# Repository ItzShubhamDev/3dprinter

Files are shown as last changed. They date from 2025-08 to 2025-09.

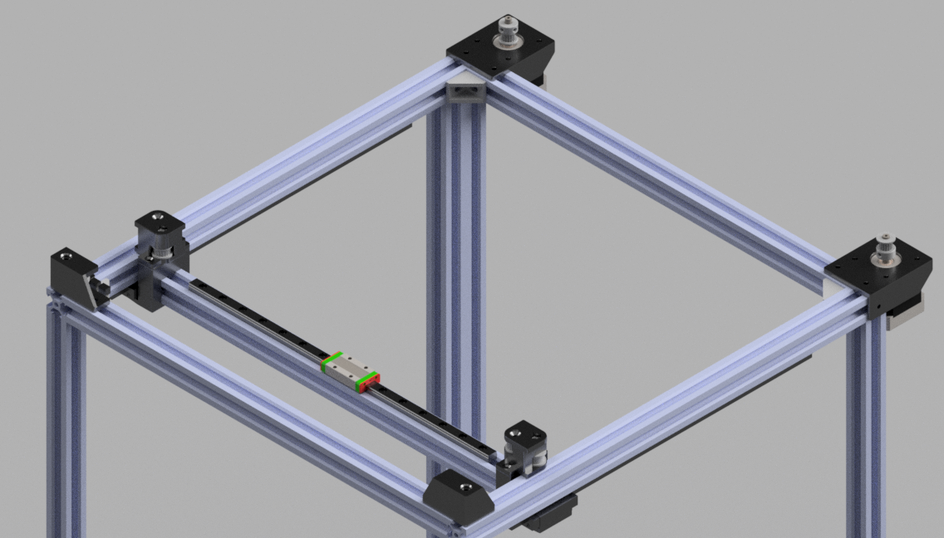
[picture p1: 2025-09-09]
images/8.png

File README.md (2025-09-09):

# Yenvo X3

A Custom Large CoreXY 3D Printer having a Print Volume of 36,000 cm³ powered by Bigtreetech SKRat V1.0 and Marling firmware.

My and my friend wanted to print something large without sliccing it, so I decided to make this printer as part of Highway.
This repository contains information related to 3D Printer, including the 3D parts models, firmware, BOM, all models imported into the design.

## Features

- **Faster building** - CoreXY printers are in general faster than Cartesian printers
- **Less space** - Unlike Cartesian printers in which Z-axis moves horizonatally, Z-axis moves vertically so it takes less space
- **Large build area 300x300x400 mm³** - Common printers around this price are mostly 250³ mm³.
- **Easy to maintain and upgrade** - If anything gives wrong just replace that part.
- **Budget friendly** - Only around 300$ can be reduced more if in a metro city by buying parts locally.

### Printer







### Structure 



### Z-Axis



### XY Motion



### Print Area



### Motherboard, Power Supply and Display



## Bill Of Materials

|Name |Quantity|Price(INR)|Cost(INR)|Cost(USD)|Source |
|---|---|---|---|---|---|
|Titan extruder kit 0.4mm Mk8 nozzle 1.75mm filament for 3D printer|1 |2199 |2199 |24.189 |https://novo3d.in/titan-extruder-kit/ |
|42 stepper motor nema17 40mm for 3D printer |4 |579 |2316 |25.476 |https://novo3d.in/42-stepper-motor-nema17/ |
|Aluminium Profiles 2020 V Slot Extrusion black anodized - 380mm |6 |136.01 |816.08 |8.97688  |https://novo3d.in/aluminium-profiles-2020/ |
|Aluminium Profiles 2020 V Slot Extrusion black anodized - 480mm |4 |171.81 |687.23 |7.55953  |https://novo3d.in/aluminium-profiles-2020/ |
|Aluminium profile 2040 V Slot extrusion black anodized - 460mm |1 |390.54 |390.54 |4.29594  |https://novo3d.in/aluminium-profile-2040/ |
|Aluminium Profiles 2020 V Slot Extrusion black anodized - 420mm |2 |150.33 |300.66 |3.30726  |https://novo3d.in/aluminium-profiles-2020/ |
|Linear Guide Rail MGN Blocks CNC Linear Rail Slide - MGN12H |2 |499 |998 |10.978 |https://novo3d.in/linear-guide-rail/?attribute_type=MGN12H |
|MGN12H Linear Rail Guide Carriage 30cm (without block) |2 |849 |1698 |18.678 |https://novo3d.in/mgn12h-linear-rail/?attribute_size=30cmattribute_type=without+block |
|MGN9H Linear Rails 30cm (without block) |1 |799 |799 |8.789 |https://novo3d.in/mgn9h-linear-rail/?attribute_length=30cmattribute_block=without+block |
|Linear Guide Rail MGN Blocks CNC Linear Rail Slide - MGN9H |1 |479 |479 |5.269 |https://novo3d.in/linear-guide-rail/?attribute_type=MGN9H |
|10mm Smooth Rod Stainless Steel - 500mm |4 |265 |1060 |11.66 |https://novo3d.in/10mm-smooth-rod/?attribute_length=500mm |
|Flexible coupling 5x8mm |2 |55 |110 |1.21 |https://novo3d.in/flexible-coupling-5x8mm/ |
|LM10UU 10mm linear bearing |4 |45 |180 |1.98 |https://novo3d.in/lm10uu-10mm-bearing/ |
|Single Start Lead Screw 2mm pitch - 400mm |2 |239 |478 |5.258 |https://novo3d.in/single-start-lead-screw/?attribute_size=400mm |
|GT2 6mm Timing belt Steel Core - 1000cm |1 |690 |690 |7.59 |https://novo3d.in/gt2-6mm-belt/ |
|Motor Pulley GT2 16 teeth 5mm bore |2 |35 |70 |0.77 |https://novo3d.in/motor-pulley/?attribute_no-of-teeth=16+teethattribute_bore=5mm |
|Idler pulley 6mm without teeth 5mm bore |2 |69 |138 |1.518 |https://novo3d.in/idler-pulley/?attribute_type=6mm+without+teeth |
|Idler pulley 6mm with teeth 5mm bore |6 |69 |414 |4.554 |https://novo3d.in/idler-pulley-6mm/?attribute_belt-width=6mm+with+teeth |
|Mini Limit Switch 3 pin SPDT L-type |3 |13.5 |40.5 |0.4455 |https://novo3d.in/mini-limit-switch/?attribute_type=L-+type |
|Bigtreetech Mini 12864 Display V2.0 |1 |1099 |1099 |12.089 |https://novo3d.in/bigtreetech-mini-12864-display/ |
|Bigtreetech SKRat V1.0 control board 32bit 64MHz |1 |3689 |3689 |40.579 |https://novo3d.in/bigtreetech-skrat-v1-0/ |
|Bed Leveling Nut Set M3 |4 |29 |116 |1.276 |https://novo3d.in/bed-leveling-nutset/?attribute_type=M3+nut+set |
|Heat bed 310mm 12V with 100cm cable |1 |1799 |1799 |19.789 |https://novo3d.in/heat-bed-310mm/?attribute_voltage=12vattribute_type=Heat+bed+with+100cm+cable|
|Meanwell Power Supply 12V 30A |1 |2999 |2999 |32.989 |https://novo3d.in/mean-well-power-supply/?attribute_voltage=12V+30A |
|Misc. (Screw, Nuts, Bolts, Wires, etc.) |1 | | |25 | |
| | | |23566.01 |284.22611| |

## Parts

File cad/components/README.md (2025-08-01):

## Models Info 

### Created By Me

- 5mmx8mm Coupling Shaft
- 8mm Threaded Rod 400mm
- 10mm Smooth Rod 500mm
- Brass Circle Nut
- Display
- Double Head Pulley Holder
- Extruder Motor Holder
- GT2 20 Teeth
- Hotend Extruder joint
- Hotend Holder
- Hotend Stand
- Idle Pulley 20 teeth
- L Joint
- LM10UU
- Motor Holder
- Sensor Case Z
- Sensor Case
- SK10 Shaft
- Teethless Pulley
- XY Joint
- Z Motion Motor Holder

### Modified By Me

- 2020 Aluminium Profile
- 2040 Aluminium Profile
- MGN9H
- MGN12C_With_Rail
- NEMA 17

### External

- 4010 - Blower Assembly
- Bigtreetech Mini12864 V1.0-3D
- Bondtech dual gear extruder
- D2F-01L
- EL90050--STD--24V 360W Power Supply 
- V6 Short Highspeed Hotend v10

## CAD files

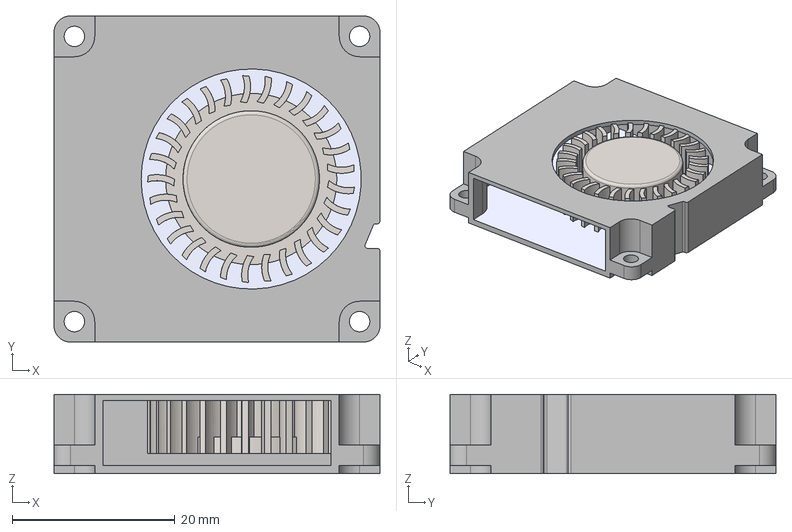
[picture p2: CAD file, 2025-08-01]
cad/components/4010 - Blower Assembly.step
40.0 x 40.0 x 9.75 mm

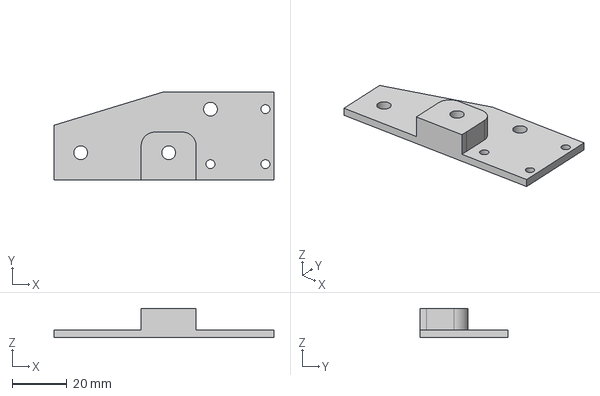
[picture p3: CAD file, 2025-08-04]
cad/components/Pulley Joint.step
80.0 x 32.2 x 10.6 mm

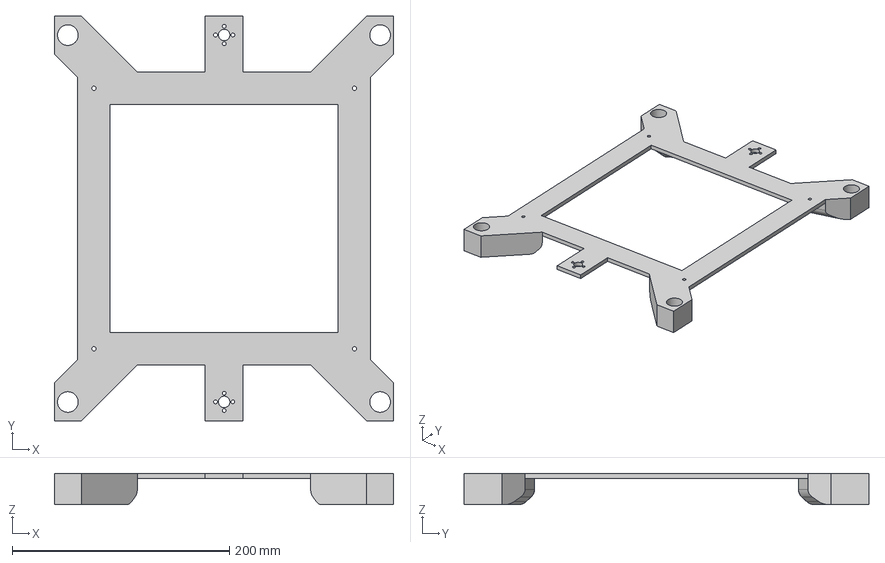
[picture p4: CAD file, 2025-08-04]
cad/production/Heatbed support.step
312.7 x 373.1 x 29.0 mm

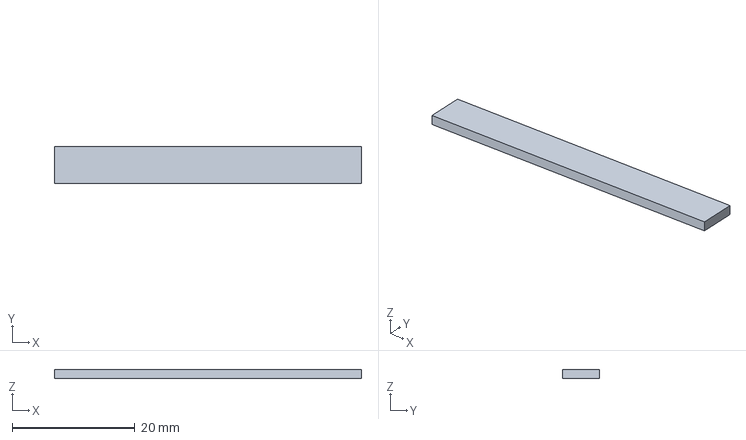
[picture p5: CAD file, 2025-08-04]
cad/components/Simple Belt.step
50.0 x 6.00 x 1.50 mm

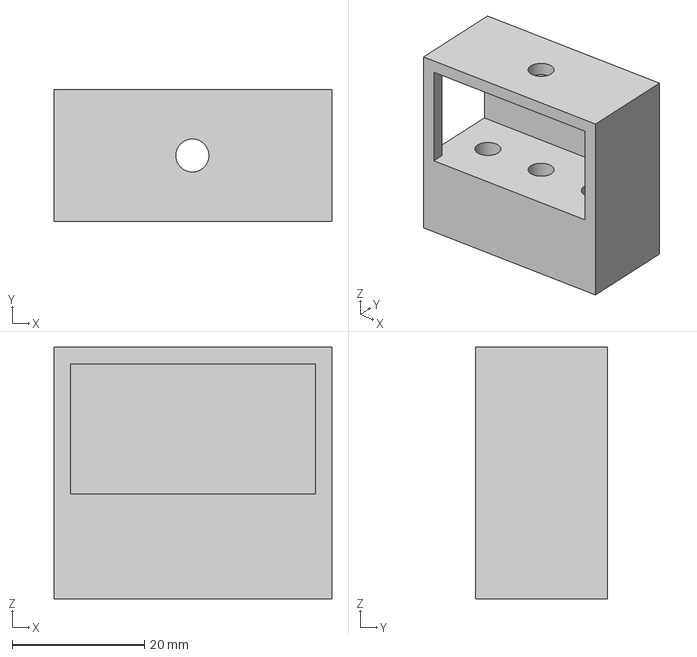
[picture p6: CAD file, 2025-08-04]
cad/production/Pulley Case.step
42.0 x 20.0 x 38.0 mm

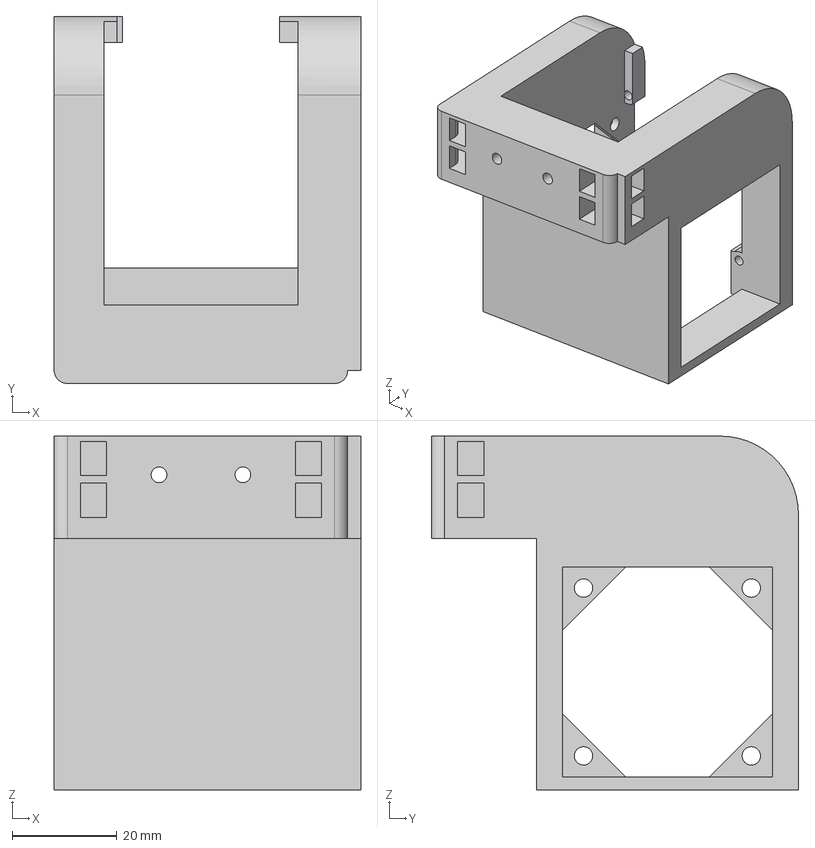
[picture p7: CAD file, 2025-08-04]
cad/components/Hotend Case.step
58.5 x 70.0 x 67.5 mm

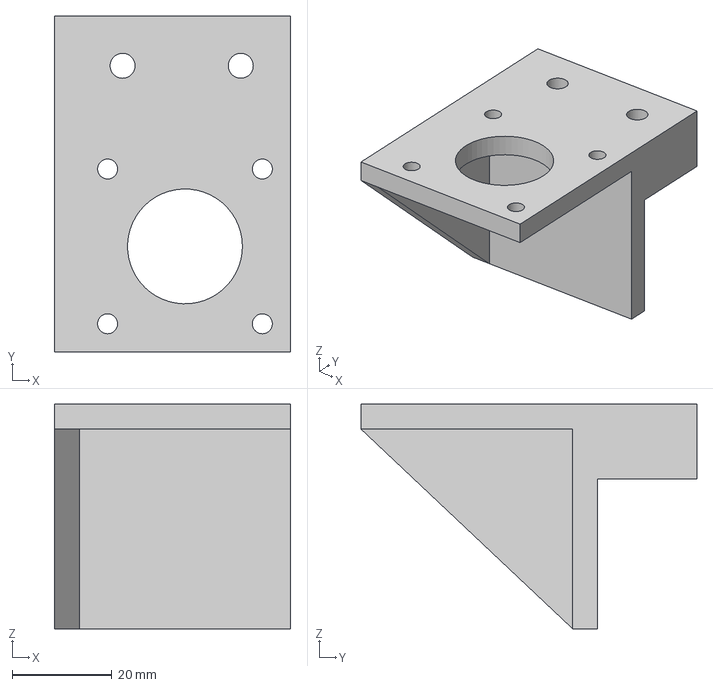
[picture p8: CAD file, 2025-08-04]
cad/components/Nema17 Holder.step
47.3 x 67.3 x 45.0 mm

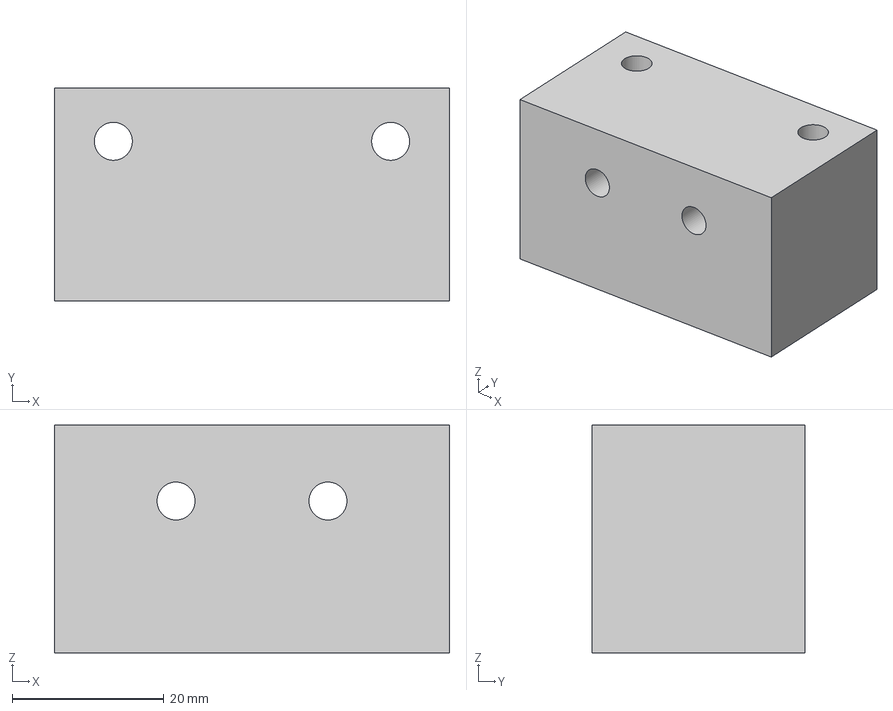
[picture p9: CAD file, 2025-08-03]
cad/production/KFL08Joint.step
52.0 x 28.0 x 30.0 mm

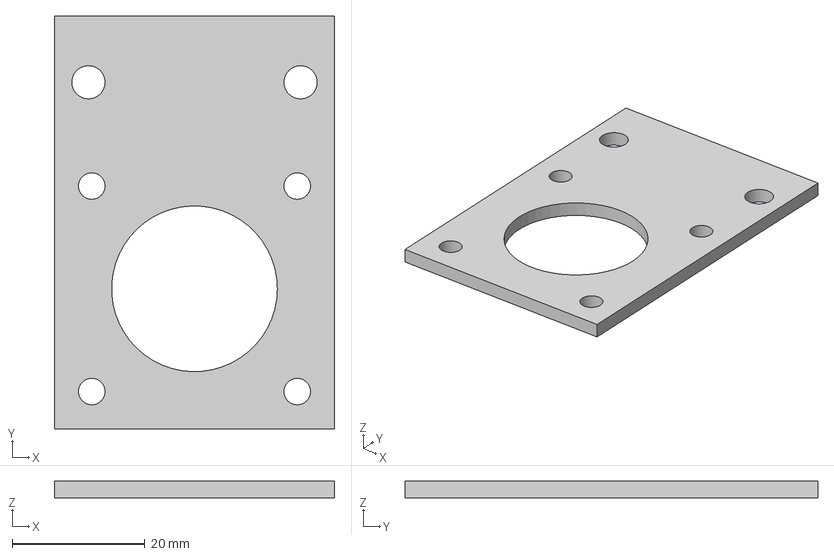
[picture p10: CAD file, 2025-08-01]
cad/production/Z Motion Motor Holder.step
42.3 x 62.3 x 2.50 mm

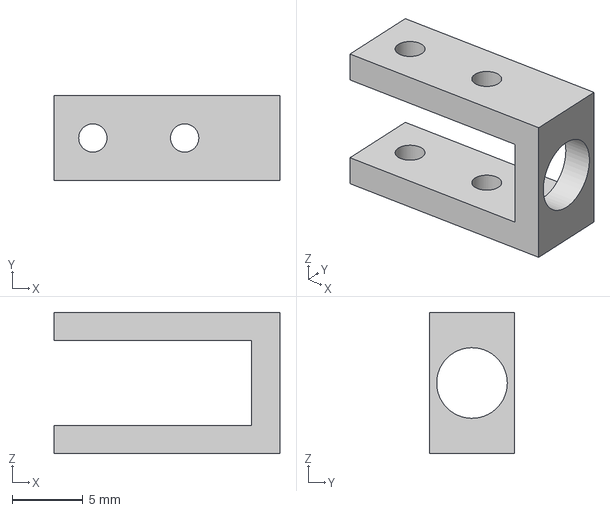
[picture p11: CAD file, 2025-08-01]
cad/production/Sensor Case.step
16.0 x 6.00 x 10.0 mm

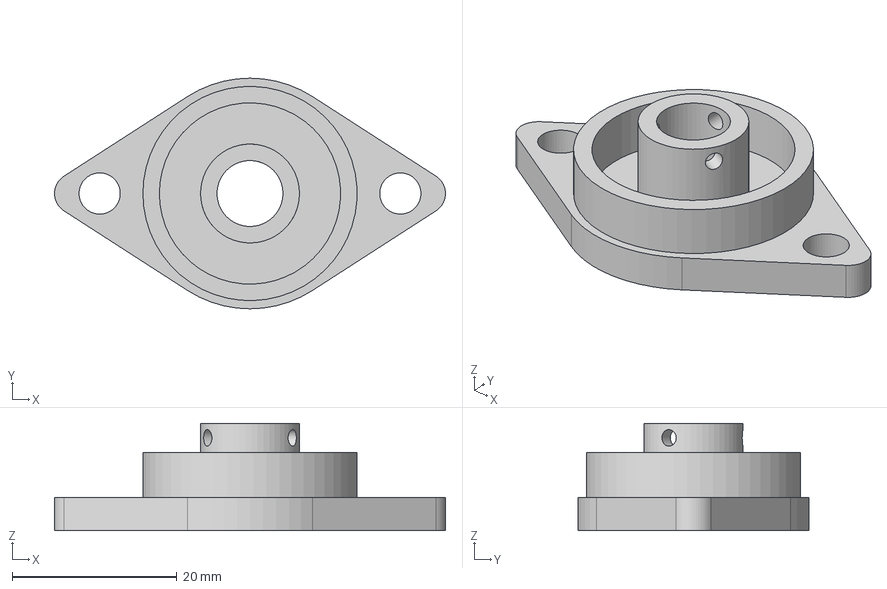
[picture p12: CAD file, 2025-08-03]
cad/components/KFL08.step
47.5 x 28.0 x 13.0 mm

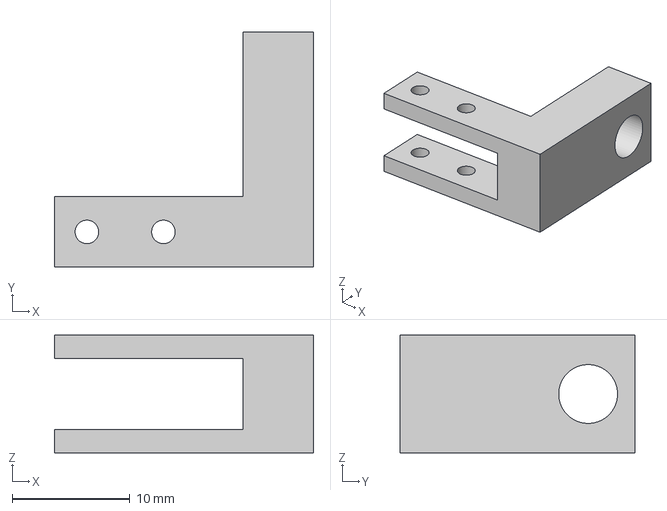
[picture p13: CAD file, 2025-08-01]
cad/production/Sensor Case Z.step
22.0 x 20.0 x 10.0 mm

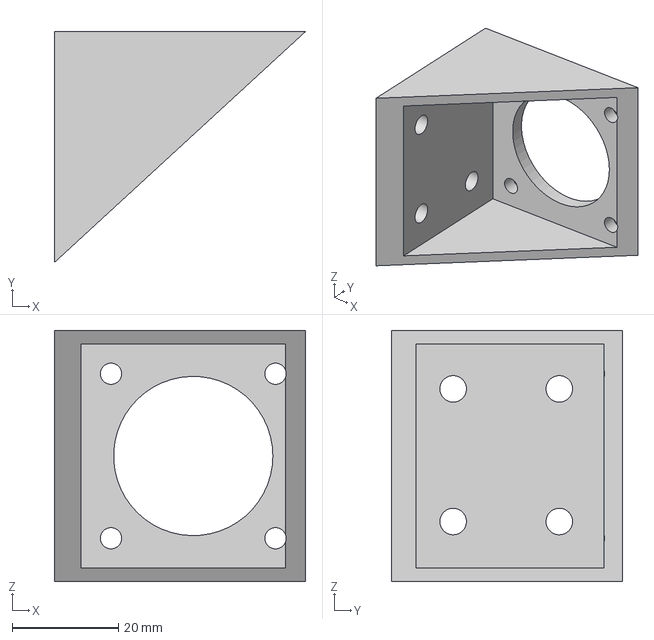
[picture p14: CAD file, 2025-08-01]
cad/production/Extruder Motor Holder.step
47.3 x 43.5 x 47.3 mm

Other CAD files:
cad/components/10mm Smooth Rod 500mm.step
cad/components/2020 Aluminium Profile.step
cad/components/2040 Aluminium Profile.step
cad/components/5mmx8mm Coupling Shaft.step
cad/components/8mm Threaded Rod 400mm.step
cad/components/Brass Circle Nut.step
cad/components/D2F-01L.step
cad/components/GT2 20 Teeth.step
cad/components/Hotend Extruder joint.step
cad/components/Hotend Stand.step
cad/components/Idle Pulley 20 teeth.step
cad/components/L Joint.step
cad/components/LM10UU.step
cad/components/MGN12C_With_Rail.step
cad/components/MGN9H.step
cad/components/NEMA 17.step
cad/components/Nema17 Holder (1).step
cad/components/Pulley Case (1).step
cad/components/Pulley Joint (1).step
cad/components/SK10 Shaft.step
cad/components/Teethless Pulley.step
cad/production/Nema17 Holder (1).step
cad/production/Pulley Case (1).step

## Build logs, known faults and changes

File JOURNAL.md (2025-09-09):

---
Title: "Yenvo X3"
Author: "Shubham"
Description: "A CoreXY 3D Printer having a large build volume 300x300x400 mm³"
Created_at: "2024-07-28"
Total Time Spent: 95 hours
---

# Yenvo X3

## Overview

| Section | Details |
| --- | --- |
| Design Choices | Decided to go with **CoreXY** over Cartesian / Delta printer for a combination of speed and stability.<br/> Wanted to make a large **400x400x400 mm³** printer but limited to **300x300x400 mm³** due to unavailibity of large heatbeds still enabling printing large parts without joints. <br /> Decided to use **2020 and 2040** Aluminium Extrusions for the sturcture to provide structural rigidity and ease to joints. <br /> Initially thought on using **V-Wheels** for the XY motion, went with **Linear Rails** after learning about the drawbacks of using V-Wheels. <br /> Used **2x Lead Screw Threaded Rods** both joint with one stepper motor each along with **4x Smooth Rods** for the movement of Z-Axis. <br /> For the movement of Hotend assembly along X-axis decided to go with **Linear Rails** too might be an overkill but would provide much precise movement <br /> For the extruder favoured went with **Direct drive**. <br /> As for the hotend, I would most likely be using a **0.4mm Volcano Hotend** to allow fast print times fitting the large build volume. <br /> As for the motherboard I would most likely be using [SKRat V1](https://novo3d.in/bigtreetech-skrat-v1-0/) due to it's pricing and connectors for 2 Z-Axis motors (which I might add in future) or [SKR MINI E3 V3](https://novo3d.in/skr-mini-e3/) which doesn't have separate connections for 2 Z-Axis motors but supports parallel connection with same pricing as SKRat V1 and additional silent features and larger heat sink for better heat management. |
| Challenges Faced | The most problematic issue I faced was **Components Sourcing**, whenever I decided to go with a part either it was unavailable or was for ridiculous high price on the local vendors. And purchasing them overseas although cheaper would end up being higher price due to shippings and customs. <br /> The second problem I faced was dimensions issue since at start I had no idea what the dimensions would each part be, I had to made some changes almost every time I added a new component.|
| References | I got to learn a lot about CoreXY Printers builds from amazing videos like [TechBuilder's DIY Guide](https://www.youtube.com/watch?v=yuAN5AzEWCg) and [3DJake's DIY Guide](https://www.youtube.com/watch?v=NMfFirtB1D4), apart from these I also watched and read articles few more to learn more. <br /> I also used some 3D models from [GrabCAD](https://grabcad.com/). |
| Learning | Throughout the whole build I learnt a lot more about Fusion 360, how to use each and every tools. Apart from that I also learned how to design sketches effectively for an easier 3d model. Not only that I also got to know how to manage various instances of same component without creating a link between them. |

## Journal

### Day 1 (28 July)

**Log 1** - Started the day by gathering a brief information on different types of 3D Printers, their advantages, disadvantages and working principle. (CoreXY, Cartesian, Delta, etc.). Initially thought of making a large size printer 400x400x400 mm³ CoreXY printer due to high speeds prints but was restricted to 300x300 mm² beds, so ended up with 300x300x300 mm³ still large height to allow larger builds to made without any joints. Gained a lot of information from various sources especially
[TechBuilder's CoreXY Guide](https://www.youtube.com/watch?v=yuAN5AzEWCg) and [3DJake's CoreXY Guide](https://www.youtube.com/watch?v=NMfFirtB1D4).
Didn't did anything in CAD yet.

**Time Spent** - 8 hours

### Day 2 (29 July)

**Log 1** - Watched some more tutorials, regarding different CoreXY builds, component placements and different parts that can be used for getting the same effect. After some discussion with one of my friends, I decided to go with a 300x300x400 mm³ with the same bed size but still allowing models upto 400mm print without joints.

As for the CAD I started making up the basic structure of the Printer by using just basic cuboids.



**Time Spent** - 6 hours

**Log 2** - After the basic structure completed, I redesigned the base structure with the use of 8x 2020 for the base and the height and 4x 2040 Aluminium Profiles for the top..
 


**Time Spent** - 4 hours

### Day 3 (30 July)

**Log 1** - Added the Stepper Motors, Shafts and 400mm Threaded Rods. The threaded rods appreared to be at height higher than the profiles due to starting ~50-60mm above ground surface because of the motor and shaft.
So recreated the structure with more height in the Z Axis. And created some 3D models for the Linear shafts.





**Time Spent** - 5 hours

**Log 2** - After looking out various Gantries I decided to make my printer unique by using V-Wheels instead of linear rails as I was already using Aluminium Profiles and linear rails were also very expensive.

Added linear Smooth rods and shafts. <br />
Create wheels model and added the wheels, also added the plates for the wheels.
Added 300mm Aluminium Profile which felt short which I would be fixing tommorrow.




**Time spent** - 5 hours

### Day 4 (31 July)

**Log 1** - As the 300mm Aluminium Profile felt short, adjusted it's length and created and added linear rails on side of the Aluminium profile, for the movement of hotend assembly on the X-Axis.
And created L-Joints for the corners.





**Time spent** - 5 hours

**Log 2** - While gathering more information about V-wheels mouting and proper usage, found out many resources recommending not to use V-wheels for XY motions due to their bad performance and wear-tear, which makes sense why no one used V-wheels in the first place, so I eventually decided to go with the linear rails.
Had to recontruct from scratch in a new Document due to the fact components were linked and couldn't resize components at different places.

        


**Time spent** - 4 hours

**Log 3** -
Created 3 models for the pulleys required.
The Pulleys section filled up a lot of confusion inside me, I was to search for Idler Teeth Pulley, but was just searching Teeth Pulley, which I never found. After releasing this I created a model for the Idler teeth pulley as well.





**Time spent** - 4 hours

**Log 4** - The 3D models for some components were missing that includes pulleys, hotend cover and some other parts too. So, I created the 3D models for them and included them into the design.



**Time spent** - 4 hours

**Log 5** - Some other components that were missing like heatbeds, linear bearing, so created and added them as well.



**Time spent** - 3 hours

## Post Submission Journals

### Day 5 (1 August)

**Log 1** - The heatbed I previously added was just a temporary and I made that it a hurry so I forgot the heatbed needs to be separated and the bottom part should be a separate entity screwed onto the Lead Screw and onto the Linear bearings. So fixed that. And also added mounting plates and brackets for the Motion and extrusions motors respectively.



**Time spent** - 4 hours

### Day 6 (3 August)

**Log 1** - The top part of the Threaded rods appeared to be flowing, so to fix that created a 3D model for threaded rod joint and a 3D printed part to screw it onto the the Aluminium profiles.



**Time spent** - 2 hours

### Day 7 (4 August)

**Log 1** - Fixed gantry by adjusting the levels of pulleys and change pulleys types. The hotend extruder also seemed very odd, so redesigned it again.
The Heatbed support felt a bit wierd when I thought of thier movement, so decided to extend the base to cover the full motion bearings

**Time Spent** - 7 hours




### Day 8 (1 September)

**Log 1** - After being called out, fixed some components, added filament spools holder, made a case / holder for power supply and added a mounting plate for the controller board.

**Time Spent** - 6 hours





### Day 9, 10, 11 & 12  

**Time Spent** - 25 hours

My current model had a flaws so I recreated the whole model by improving and implementing a lot of changes which could have severily impacted the performance and/or functioning of the printer which includes but are not limited to:
- Split all non printable parts into 2 halves.
- Modified the Heat bed support plate
- Modified the case for Display
- Redesigned the gantry, inspired by a 3d printer built in real life and working smoothly
- Removed support from leadscrew
- Switched to Direct drive instead of Bowden drive
and a various small changes.

Special thanks to Tanishq & Raygen for helping me identifing and fixed those issues.





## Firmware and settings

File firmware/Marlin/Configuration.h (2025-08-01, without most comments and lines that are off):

#pragma once
#define CONFIG_EXAMPLES_DIR "Creality/Ender-3 Pro/BigTreeTech SKR Mini E3 1.0"
#define CONFIGURATION_H_VERSION 02010300
#define STRING_CONFIG_H_AUTHOR "(thisiskeithb, Ender-3 Pro)" // Original author or contributor.
  #define MOTHERBOARD BOARD_BTT_SKR_MINI_E3_V1_0
#define SERIAL_PORT 2
#define BAUDRATE 115200
#define SERIAL_PORT_2 -1
#define CUSTOM_MACHINE_NAME "Ender-3 Pro"
#define X_DRIVER_TYPE  TMC2209
#define Y_DRIVER_TYPE  TMC2209
#define Z_DRIVER_TYPE  TMC2209
#define E0_DRIVER_TYPE TMC2209
#define EXTRUDERS 1
#define DEFAULT_NOMINAL_FILAMENT_DIA 1.75
#define TEMP_SENSOR_0 1
#define TEMP_SENSOR_1 0
#define TEMP_SENSOR_2 0
#define TEMP_SENSOR_3 0
#define TEMP_SENSOR_4 0
#define TEMP_SENSOR_5 0
#define TEMP_SENSOR_6 0
#define TEMP_SENSOR_7 0
#define TEMP_SENSOR_BED 1
#define TEMP_SENSOR_PROBE 0
#define TEMP_SENSOR_CHAMBER 0
#define TEMP_SENSOR_COOLER 0
#define TEMP_SENSOR_BOARD 0
#define TEMP_SENSOR_SOC 0
#define TEMP_SENSOR_REDUNDANT 0
#define DUMMY_THERMISTOR_998_VALUE  25
#define DUMMY_THERMISTOR_999_VALUE 100
#if TEMP_SENSOR_IS_MAX_TC(0)
  #define MAX31865_SENSOR_OHMS_0      100 // (Ω) Typically 100 or 1000 (PT100 or PT1000)
  #define MAX31865_CALIBRATION_OHMS_0 430 // (Ω) Typically 430 for Adafruit PT100; 4300 for Adafruit PT1000
#endif
#if TEMP_SENSOR_IS_MAX_TC(1)
  #define MAX31865_SENSOR_OHMS_1      100
  #define MAX31865_CALIBRATION_OHMS_1 430
#endif
#if TEMP_SENSOR_IS_MAX_TC(2)
  #define MAX31865_SENSOR_OHMS_2      100
  #define MAX31865_CALIBRATION_OHMS_2 430
#endif
#if TEMP_SENSOR_IS_MAX_TC(BED)
  #define MAX31865_SENSOR_OHMS_BED      100
  #define MAX31865_CALIBRATION_OHMS_BED 430
#endif
#if HAS_E_TEMP_SENSOR
  #define TEMP_RESIDENCY_TIME         10  // (seconds) Time to wait for hotend to "settle" in M109
  #define TEMP_WINDOW                  1  // (°C) Temperature proximity for the "temperature reached" timer
  #define TEMP_HYSTERESIS              3  // (°C) Temperature proximity considered "close enough" to the target
#endif
#if TEMP_SENSOR_BED
  #define TEMP_BED_RESIDENCY_TIME     10  // (seconds) Time to wait for bed to "settle" in M190
  #define TEMP_BED_WINDOW              1  // (°C) Temperature proximity for the "temperature reached" timer
  #define TEMP_BED_HYSTERESIS          3  // (°C) Temperature proximity considered "close enough" to the target
#endif
#if TEMP_SENSOR_CHAMBER
  #define TEMP_CHAMBER_RESIDENCY_TIME 10  // (seconds) Time to wait for chamber to "settle" in M191
  #define TEMP_CHAMBER_WINDOW          1  // (°C) Temperature proximity for the "temperature reached" timer
  #define TEMP_CHAMBER_HYSTERESIS      3  // (°C) Temperature proximity considered "close enough" to the target
#endif
#if TEMP_SENSOR_REDUNDANT
  #define TEMP_SENSOR_REDUNDANT_SOURCE    E1  // The sensor that will provide the redundant reading.
  #define TEMP_SENSOR_REDUNDANT_TARGET    E0  // The sensor that we are providing a redundant reading for.
  #define TEMP_SENSOR_REDUNDANT_MAX_DIFF  10  // (°C) Temperature difference that will trigger a print abort.
#endif
#define HEATER_0_MINTEMP   5
#define HEATER_1_MINTEMP   5
#define HEATER_2_MINTEMP   5
#define HEATER_3_MINTEMP   5
#define HEATER_4_MINTEMP   5
#define HEATER_5_MINTEMP   5
#define HEATER_6_MINTEMP   5
#define HEATER_7_MINTEMP   5
#define BED_MINTEMP        5
#define CHAMBER_MINTEMP    5
#define HEATER_0_MAXTEMP 275
#define HEATER_1_MAXTEMP 275
#define HEATER_2_MAXTEMP 275
#define HEATER_3_MAXTEMP 275
#define HEATER_4_MAXTEMP 275
#define HEATER_5_MAXTEMP 275
#define HEATER_6_MAXTEMP 275
#define HEATER_7_MAXTEMP 275
#define BED_MAXTEMP      125
#define CHAMBER_MAXTEMP  60
#define HOTEND_OVERSHOOT 15   // (°C) Forbid temperatures over MAXTEMP - OVERSHOOT
#define BED_OVERSHOOT    10   // (°C) Forbid temperatures over MAXTEMP - OVERSHOOT
#define COOLER_OVERSHOOT  2   // (°C) Forbid temperatures closer than OVERSHOOT
#define PIDTEMP           // See the PID Tuning Guide at https://reprap.org/wiki/PID_Tuning
#define PID_MAX  255      // Limit hotend current while PID is active (see PID_FUNCTIONAL_RANGE below); 255=full current
#define PID_K1     0.95   // Smoothing factor within any PID loop
    #define DEFAULT_Kp  21.73
    #define DEFAULT_Ki   1.54
    #define DEFAULT_Kd  76.55
#define MAX_BED_POWER 255 // limits duty cycle to bed; 255=full current
#define MAX_CHAMBER_POWER 255 // limits duty cycle to chamber heater; 255=full current
  #define PID_FUNCTIONAL_RANGE 20 // If the temperature difference between the target temperature and the actual temperature
#define PREVENT_COLD_EXTRUSION
#define EXTRUDE_MINTEMP 170
#define PREVENT_LENGTHY_EXTRUDE
#define EXTRUDE_MAXLENGTH 600
#define THERMAL_PROTECTION_HOTENDS // Enable thermal protection for all extruders
#define THERMAL_PROTECTION_BED     // Enable thermal protection for the heated bed
#define THERMAL_PROTECTION_CHAMBER // Enable thermal protection for the heated chamber
#define THERMAL_PROTECTION_COOLER  // Enable thermal protection for the laser cooling
#define COREXY
#define ENDSTOPPULLUPS
#define X_MIN_ENDSTOP_HIT_STATE HIGH
#define X_MAX_ENDSTOP_HIT_STATE HIGH
#define Y_MIN_ENDSTOP_HIT_STATE HIGH
#define Y_MAX_ENDSTOP_HIT_STATE HIGH
#define Z_MIN_ENDSTOP_HIT_STATE HIGH
#define Z_MAX_ENDSTOP_HIT_STATE HIGH
#define I_MIN_ENDSTOP_HIT_STATE HIGH
#define I_MAX_ENDSTOP_HIT_STATE HIGH
#define J_MIN_ENDSTOP_HIT_STATE HIGH
#define J_MAX_ENDSTOP_HIT_STATE HIGH
#define K_MIN_ENDSTOP_HIT_STATE HIGH
#define K_MAX_ENDSTOP_HIT_STATE HIGH
#define U_MIN_ENDSTOP_HIT_STATE HIGH
#define U_MAX_ENDSTOP_HIT_STATE HIGH
#define V_MIN_ENDSTOP_HIT_STATE HIGH
#define V_MAX_ENDSTOP_HIT_STATE HIGH
#define W_MIN_ENDSTOP_HIT_STATE HIGH
#define W_MAX_ENDSTOP_HIT_STATE HIGH
#define Z_MIN_PROBE_ENDSTOP_HIT_STATE HIGH
#define ENDSTOP_INTERRUPTS_FEATURE
#define DEFAULT_AXIS_STEPS_PER_UNIT   { 80, 80, 1600, 96 }
#define EDITABLE_STEPS_PER_UNIT
#define DEFAULT_MAX_FEEDRATE          { 500, 500, 5, 25 }
#define DEFAULT_MAX_ACCELERATION      { 10000, 10000, 100, 5000 }
#define DEFAULT_ACCELERATION           500    // X, Y, Z and E acceleration for printing moves
#define DEFAULT_RETRACT_ACCELERATION   500    // E acceleration for retracts
#define DEFAULT_TRAVEL_ACCELERATION    500    // X, Y, Z acceleration for travel (non printing) moves
  #define JUNCTION_DEVIATION_MM 0.08  // (mm) Distance from real junction edge
  #define JD_HANDLE_SMALL_SEGMENTS    // Use curvature estimation instead of just the junction angle
#define S_CURVE_ACCELERATION
#define NOZZLE_TO_PROBE_OFFSET { 10, 10, 0 }
#define PROBING_TOOL 0
#define PROBING_MARGIN 10
#define XY_PROBE_FEEDRATE    (133*60) // (mm/min)
#define Z_PROBE_FEEDRATE_FAST  (4*60) // (mm/min)
#define Z_PROBE_FEEDRATE_SLOW (Z_PROBE_FEEDRATE_FAST / 2) // (mm/min)
#define Z_CLEARANCE_DEPLOY_PROBE   10 // (mm) Z Clearance for Deploy/Stow
#define Z_CLEARANCE_BETWEEN_PROBES  5 // (mm) Z Clearance between probe points
#define Z_CLEARANCE_MULTI_PROBE     5 // (mm) Z Clearance between multiple probes
#define Z_PROBE_ERROR_TOLERANCE     3 // (mm) Tolerance for early trigger (<= -probe.offset.z + ZPET)
#define Z_PROBE_LOW_POINT          -2 // (mm) Farthest distance below the trigger-point to go before stopping
#define X_ENABLE_ON LOW
#define Y_ENABLE_ON LOW
#define Z_ENABLE_ON LOW
#define E_ENABLE_ON LOW // For all extruders
#define INVERT_X_DIR true
#define INVERT_Y_DIR true
#define INVERT_Z_DIR false
#define INVERT_E0_DIR true
#define INVERT_E1_DIR false
#define INVERT_E2_DIR false
#define INVERT_E3_DIR false
#define INVERT_E4_DIR false
#define INVERT_E5_DIR false
#define INVERT_E6_DIR false
#define INVERT_E7_DIR false
#define X_HOME_DIR -1
#define Y_HOME_DIR -1
#define Z_HOME_DIR -1
#define X_BED_SIZE 300
#define Y_BED_SIZE 300
#define X_MIN_POS 0
#define Y_MIN_POS 0
#define Z_MIN_POS 0
#define X_MAX_POS X_BED_SIZE
#define Y_MAX_POS Y_BED_SIZE
#define Z_MAX_POS 380
#define MIN_SOFTWARE_ENDSTOPS
  #define MIN_SOFTWARE_ENDSTOP_X
  #define MIN_SOFTWARE_ENDSTOP_Y
  #define MIN_SOFTWARE_ENDSTOP_Z
  #define MIN_SOFTWARE_ENDSTOP_I
  #define MIN_SOFTWARE_ENDSTOP_J
  #define MIN_SOFTWARE_ENDSTOP_K
  #define MIN_SOFTWARE_ENDSTOP_U
  #define MIN_SOFTWARE_ENDSTOP_V
  #define MIN_SOFTWARE_ENDSTOP_W
#define MAX_SOFTWARE_ENDSTOPS
  #define MAX_SOFTWARE_ENDSTOP_X
  #define MAX_SOFTWARE_ENDSTOP_Y
  #define MAX_SOFTWARE_ENDSTOP_Z
  #define MAX_SOFTWARE_ENDSTOP_I
  #define MAX_SOFTWARE_ENDSTOP_J
  #define MAX_SOFTWARE_ENDSTOP_K
  #define MAX_SOFTWARE_ENDSTOP_U
  #define MAX_SOFTWARE_ENDSTOP_V
  #define MAX_SOFTWARE_ENDSTOP_W
#define MESH_BED_LEVELING
  #define MANUAL_PROBE_START_Z 0.2  // (mm) Comment out to use the last-measured height
  #define ENABLE_LEVELING_FADE_HEIGHT
    #define DEFAULT_LEVELING_FADE_HEIGHT 10.0 // (mm) Default fade height.
  #define SEGMENT_LEVELED_MOVES
  #define LEVELED_SEGMENT_LENGTH 5.0 // (mm) Length of all segments (except the last one)
  #define MESH_INSET 10          // Set Mesh bounds as an inset region of the bed
  #define GRID_MAX_POINTS_X 3
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

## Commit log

2025-08-01 Add all files!
    [10mm Smooth Rod 500mm.step, 2020 Aluminium Profile.step, 2040 Aluminium Profile.step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]
2025-08-03 Add support for threaded rods
    [KFL08.step, KFL08Joint.step]
2025-08-04 Fixed issues related to pulleys. And some minor changes
    [Double Head Pulley Holder (1).step, Double Head Pulley Holder.step, Heatbed support.step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]
2025-08-04 Restore render images
    [Pulley Joint (1).step, Pulley Joint.step]
2025-09-01 Added filament holder, controller board plate and power supply plate.
2025-09-02 Update cad files.
2025-09-04 Updated cad files
2025-09-08 Rebuilt the Printer fixing a lots of issues
2025-09-08 Update BOM
    [bom.csv]

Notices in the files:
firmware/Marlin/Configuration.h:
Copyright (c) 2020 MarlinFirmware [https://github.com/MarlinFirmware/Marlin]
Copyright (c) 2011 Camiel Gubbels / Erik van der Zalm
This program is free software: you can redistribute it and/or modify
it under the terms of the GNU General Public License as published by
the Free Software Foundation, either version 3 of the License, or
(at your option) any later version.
